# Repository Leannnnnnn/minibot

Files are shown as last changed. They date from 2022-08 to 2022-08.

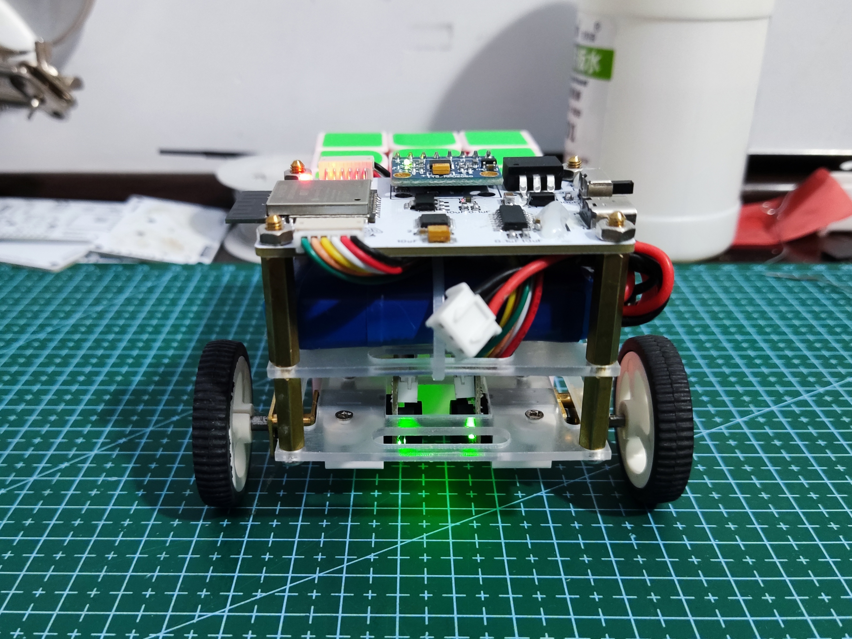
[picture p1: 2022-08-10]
doc/img/6.jpg

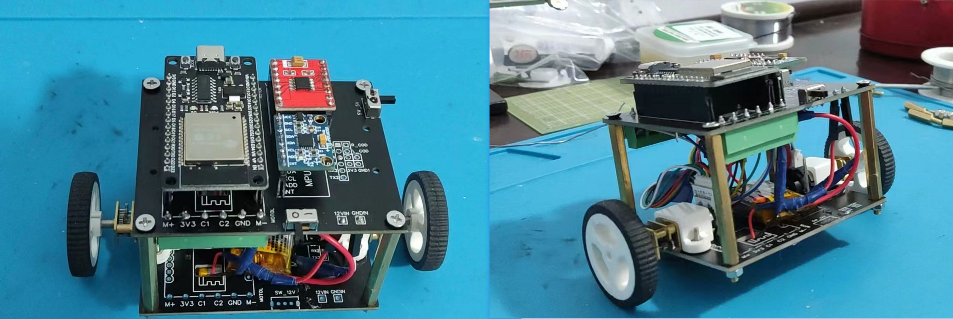
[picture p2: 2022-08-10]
doc/img/8png.png

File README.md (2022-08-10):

# minibot

> 最新内容在master分支\
> 详细说明请查看立创开源链接：[https://oshwhub.com/leannn/minibot](https://oshwhub.com/leannn/minibot)

## 1.项目介绍
### 1.0 前言
平衡车几乎是每个人入坑电子DIY的必做项目，包括了传感器采集处理、电机运动控制、pid算法调节等许多领域，同时兼顾专业性和趣味性，非常适合作为入门练习项目。本项目经过几次版本迭代（见后续介绍），最后确定为当前的形态，在外形结构和软件控制方面实现了比较好的平衡，外观小巧，运动性能卓越。

### 1.1 基本介绍
使用ESP32-WROOM作为主控芯片，MPU6050六轴加速度传感器模块获取姿态信息，DRV8833芯片驱动电机运动，提供较大电流，电机选用N20减速电机，带有AB相霍尔编码器用于测量转速。供电方面选用7.4V锂电池(2s)，经三端线性稳压器LM1084稳压至5V再使用1117稳压至3.3V给ESP32供电。

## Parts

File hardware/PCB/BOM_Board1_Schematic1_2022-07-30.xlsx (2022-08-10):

No. | Quantity | Device | Designator | Footprint | Value | Manufacturer Part | Manufacturer | Supplier Part | Supplier | Pins
1 | 3 | CAP_0603 | C1,C6,C13 | C0603 | 100nF |  |  |  |  | 2
2 | 5 | CAP_0603 | C2,C3,C5,C7,C9 | C0603 | 10uF |  |  |  |  | 2
3 | 1 | CAP_1206 | C4 | C1206 | 22uF |  |  |  |  | 2
4 | 1 | CAP_0603 | C8 | C0603 | 0.1uF |  |  |  |  | 2
5 | 1 | CAP_0603 | C10 | C0603 | 1uF |  |  |  |  | 2
6 | 1 | CAP_0603 | C11 | C0603 | 2.2uF |  |  |  |  | 2
7 | 1 | CAP_0603 | C12 | C0603 | 10nF |  |  |  |  | 2
8 | 2 | ZH1.5-6AW | CN1,CN2 | CONN-TH_ZH1.5-6AW |  | ZH1.5-6AW | CAX(创都) | C722927 | LCSC | 6
9 | 1 | SS14S-SMA | D1 | SMA_L4.3-W2.6-LS5.0-RD |  | SS14S-SMA |  | C9900003094 | LCSC | 2
10 | 1 | A2541WV-2P | H1 | HDR-TH_P2.54-H-M_A2541WV-2P |  | A2541WV-2P | CJT(Changjiang Connectors) | C225477 | LCSC | 2
11 | 1 | LED_0603-R | LED1 | LED0603-RD_BLUE |  |  |  | C72044 |  | 2
12 | 2 | 2N3904(SOT-23) | Q1,Q2 | SOT-23-3_L2.9-W1.3-P1.90-LS2.4-TR |  |  |  |  |  | 3
13 | 4 | Res_0603 | R1,R2,R6,R7 | R0603 | 10K |  |  |  |  | 2
14 | 2 | Res_0603 | R3,R4 | R0603 | 120R |  |  |  |  | 2
15 | 1 | Res_0603 | R5 | R0603 | 1k |  |  |  |  | 2
16 | 1 | SK-12D07-L5-B | SW1 | SW-TH_SK-12D02-VG5 |  |  |  |  |  | 5
17 | 1 | ESP32-WROOM-32 | U1 | WIFIM-SMD_ESP-32S |  |  |  |  |  | 39
18 | 1 | CH340C | U2 | SOP-16_L10.0-W3.9-P1.27-LS6.0-BL |  |  |  |  |  | 16
19 | 1 | AMS1117-3.3V | U3 | SOT-223-4_L6.5-W3.5-P2.30-LS7.0-BR |  |  |  |  |  | 4
20 | 1 | C3528 | U4 | CAP-SMD_L3.5-W2.8-FD | 10uF/25V | C3528 |  | C9900021806 | LCSC | 2
21 | 1 | MPU6050 | U6 | MPU6050 |  |  |  |  |  | 8
22 | 1 | LM1084S-5.0/TR | U7 | TO-263-3_L8.6-W10.2-P2.54-LS14.4-TL |  | LM1084S-5.0/TR | HGSEMI(华冠) | C259973 | LCSC | 4
23 | 1 | DRV8833PWP | U8 | ETSSOP-16_L5.0-W4.4-P0.65-LS6.4-BL-EP |  | DRV8833PWP | TI(德州仪器) | C1556089 | LCSC | 17
24 | 1 | TYPEC-304-BCP16 | USB1 | USB-C-SMD_TYPEC-304-BCP16 |  |  |  |  |  | 16

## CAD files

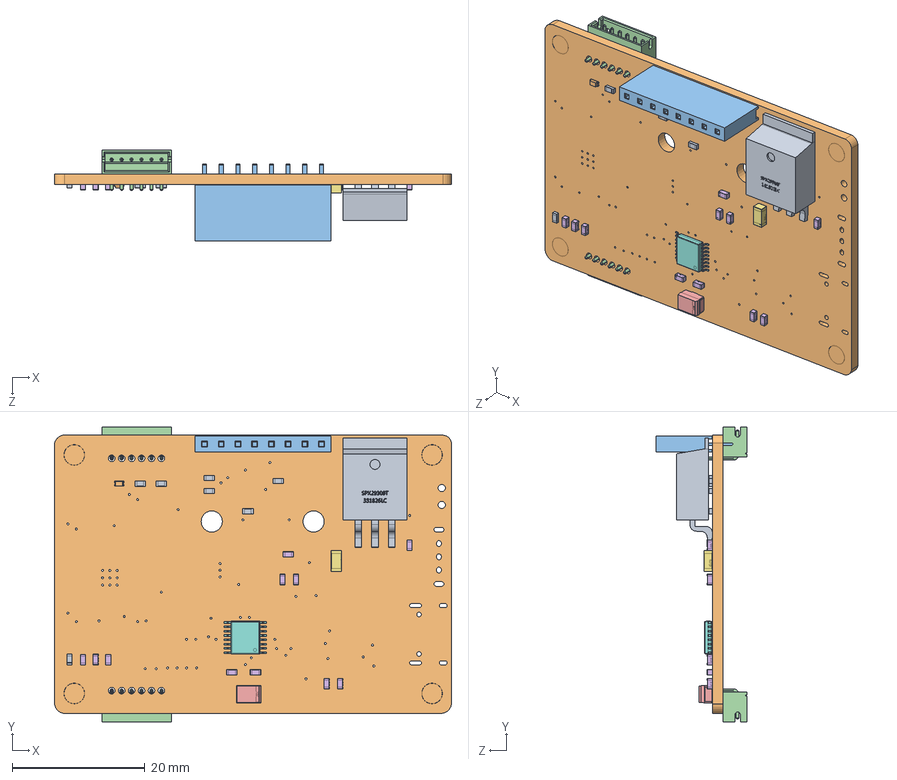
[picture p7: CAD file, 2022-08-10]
hardware/3D model/source/3D_PCB.SLDASM
59.9 x 44.5 x 13.7 mm
COMPOUND.step x 7
COMPOUND-0.step
SOLID.step
SOLID-1.step x 2
COMPOUND-2.step
=_[0_1_1_27].step x 11
=_[0_1_1_41].step
SOLID-3.step
COMPOUND-4.step
COMPOUND-5.step

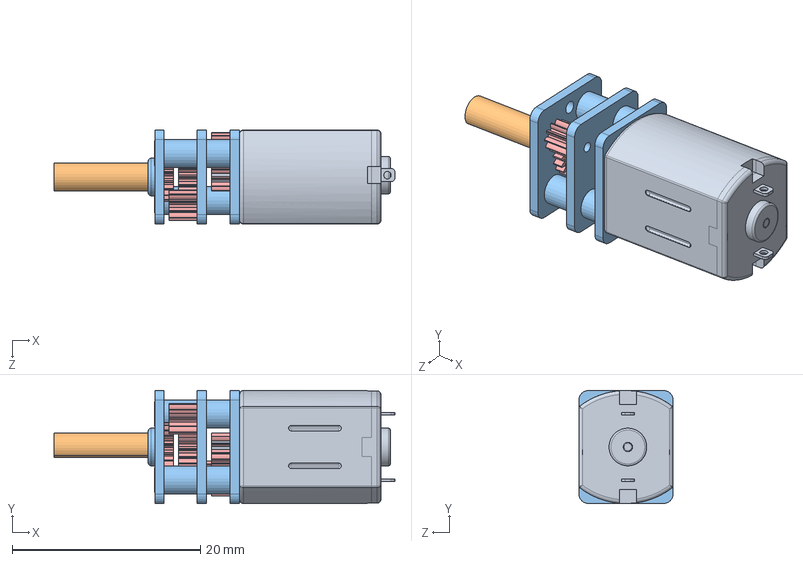
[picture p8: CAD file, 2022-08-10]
hardware/3D model/source/N20 Micro Metal Gearmotor 微型减速电机/n20 motor.SLDASM
36.2 x 12.0 x 10.0 mm
motor
n20_shaft
n20_gearbox
cross recessed countersunk head screws gb1 x 2
spur gear_gb x 6

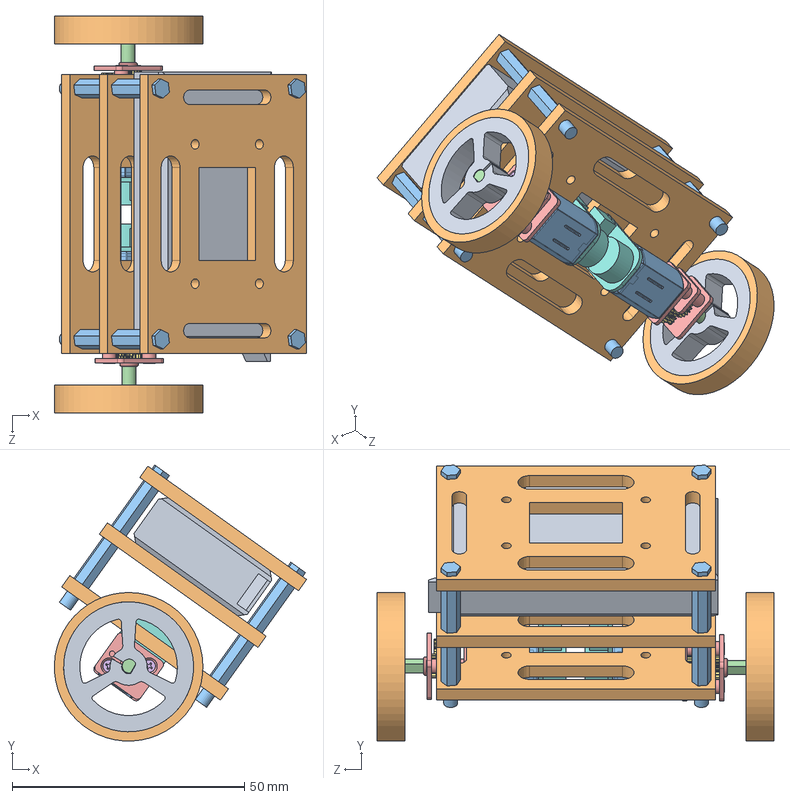
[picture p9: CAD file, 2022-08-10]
hardware/3D model/轮胎整体.SLDASM
54.3 x 59.4 x 85.4 mm
轮胎 x 2
轮胎外胎 x 2
motor x 2
n20_shaft x 2
n20_gearbox x 2
cross recessed countersunk head screws gb1 x 4
spur gear_gb x 12
零件5 x 2
电池2S
底板 x 3
铜柱 x 4

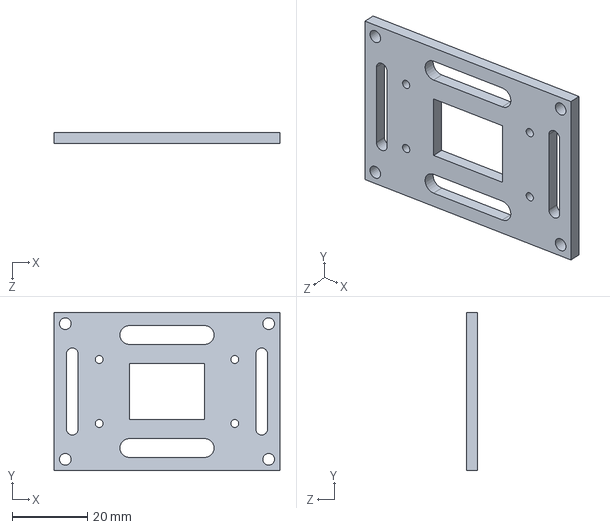
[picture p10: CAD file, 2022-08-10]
hardware/3D model/底板.SLDPRT
60.0 x 42.0 x 3.00 mm

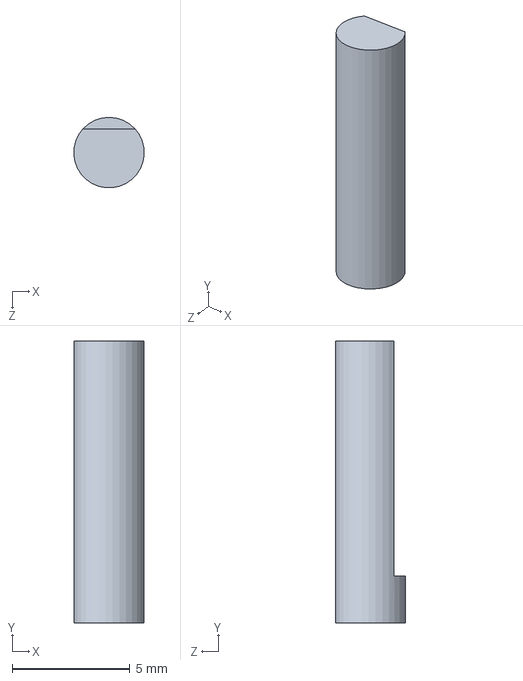
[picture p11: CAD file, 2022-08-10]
hardware/3D model/source/N20 Micro Metal Gearmotor 微型减速电机/n20_shaft.SLDPRT
3.00 x 12.0 x 2.99 mm

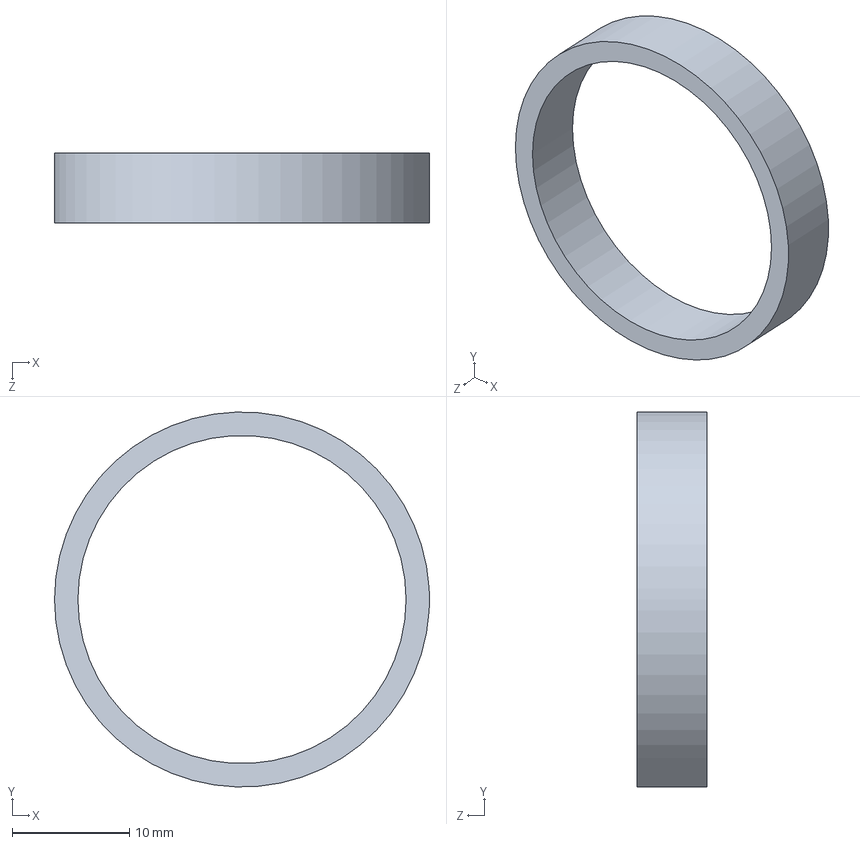
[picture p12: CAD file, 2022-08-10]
hardware/3D model/轮胎外胎.SLDPRT
32.0 x 32.0 x 6.00 mm

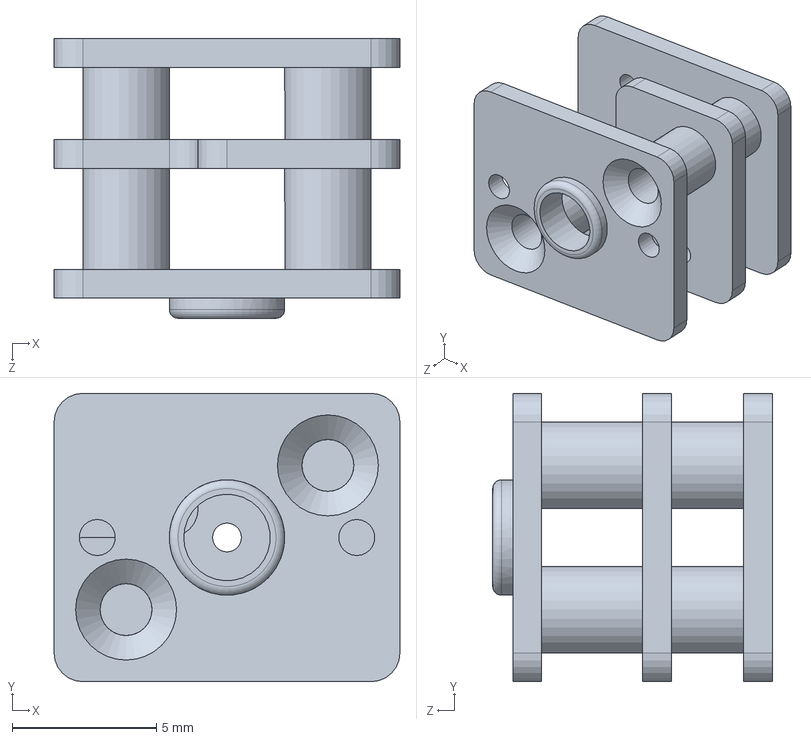
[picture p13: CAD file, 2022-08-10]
hardware/3D model/source/N20 Micro Metal Gearmotor 微型减速电机/n20_gearbox.SLDPRT
12.0 x 10.0 x 9.70 mm

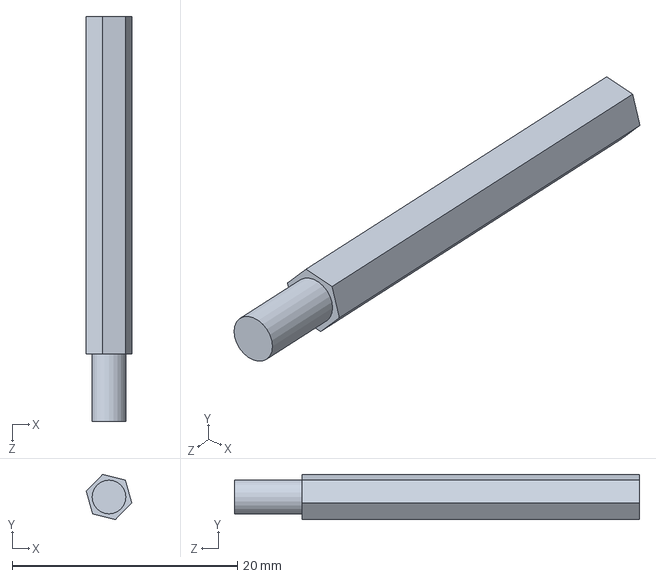
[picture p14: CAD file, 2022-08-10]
hardware/3D model/铜柱.SLDPRT
4.05 x 4.02 x 36.0 mm

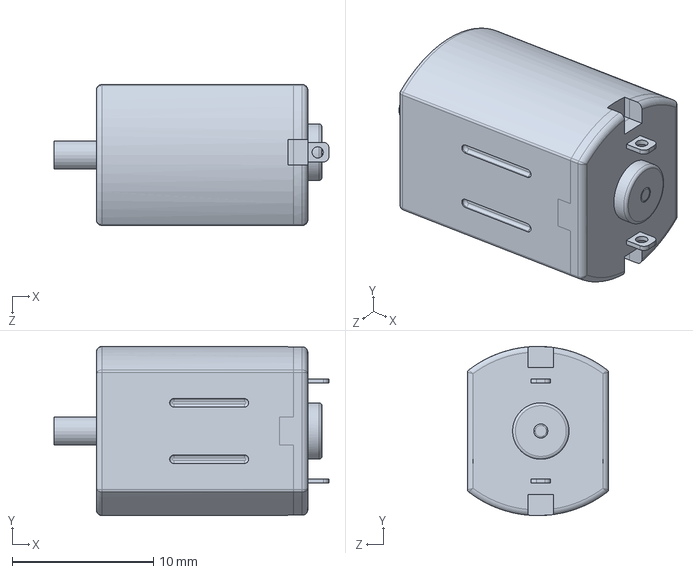
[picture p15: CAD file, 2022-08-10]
hardware/3D model/source/N20 Micro Metal Gearmotor 微型减速电机/motor.SLDPRT
19.5 x 12.0 x 10.0 mm

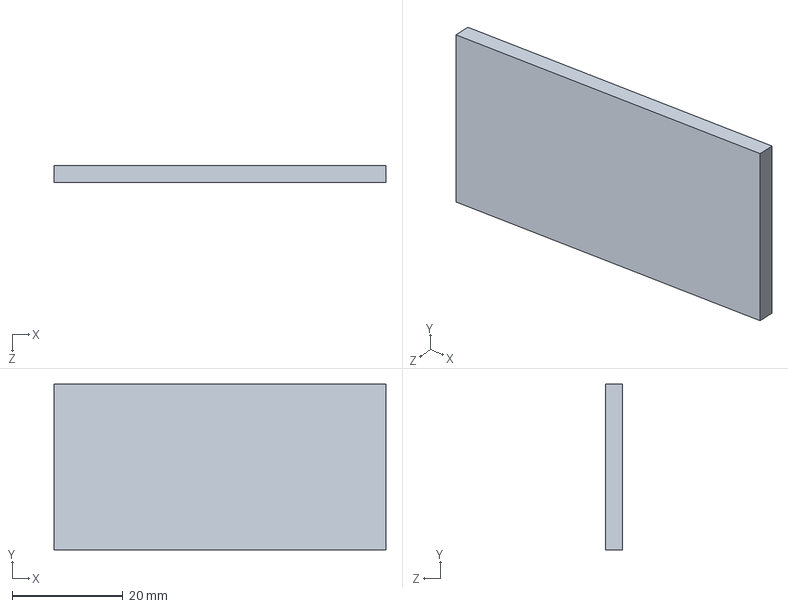
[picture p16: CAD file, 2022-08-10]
hardware/3D model/中板.SLDPRT
60.0 x 30.0 x 3.00 mm

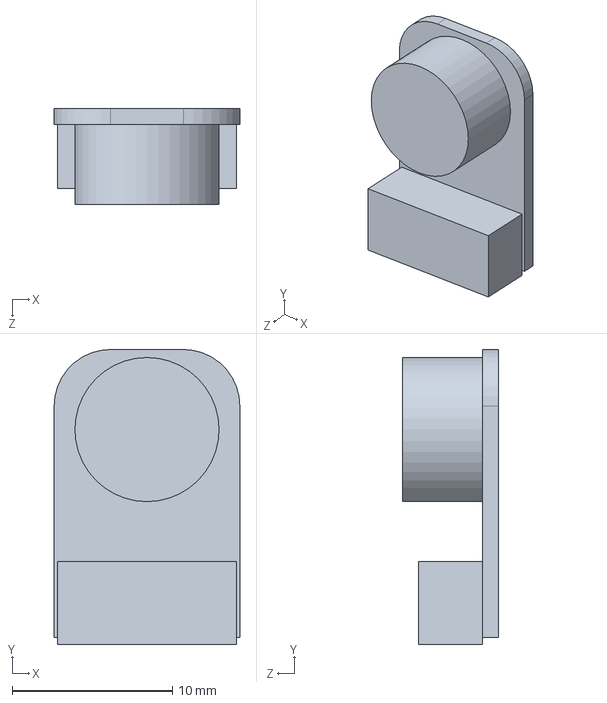
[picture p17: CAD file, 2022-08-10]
hardware/3D model/source/N20 Micro Metal Gearmotor 微型减速电机/零件5.SLDPRT
11.6 x 18.4 x 6.00 mm

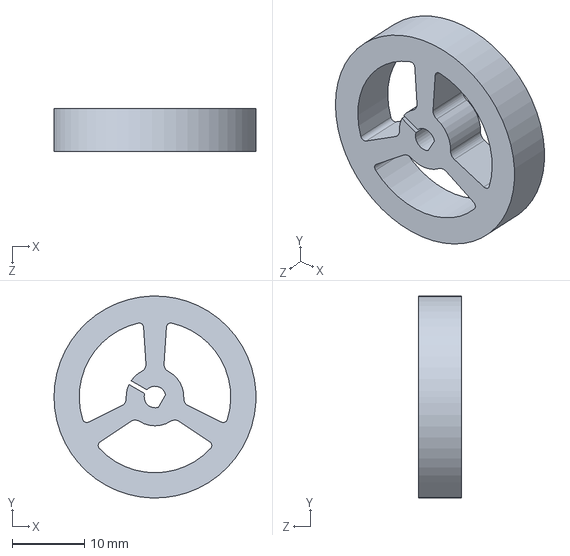
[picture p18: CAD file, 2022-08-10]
hardware/3D model/轮胎.SLDPRT
28.0 x 28.0 x 6.00 mm

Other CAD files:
hardware/3D model/source/带磁编码器的N20电机/n20ENCODED.SLDPRT
hardware/3D model/source/带磁编码器的N20电机/moto.dwg
hardware/3D model/亚克力切割.DWG
hardware/3D model/亚克力切割.SLDDRW

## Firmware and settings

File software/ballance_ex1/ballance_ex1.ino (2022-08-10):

/* ESP32平衡车miniBot
 *  
 * 平台：Arduino
 * Version: v1.1.0
 * Update: 2022-08-01
 * Author: Leannnus @bilibili.com & oshwhub.com
 * Link: https://oshwhub.com/leannn/minibot
 * 
**/


#include "PID.h"
#include <ArduinoJson.h>
#include <MPU6050_tockn.h>

#include "myBlueTooth.h"
#include "moto.h"
#include "mpu6050.h"

#define DEBUG 1  //串口输出调试信息
#define BTMODE 1 //蓝牙控制模式：0为调参模式，1为运动模式

/*************PID参数定义***********/
ArduPID pid_ang, pid_spd, pid_turn;

/*****角度环****/
double ang_set = -1.0;
double ang_in, ang_out;
double ang_p = 98.0;
double ang_i = 0.0;
double ang_d = 170.0;

/*****速度环*****/
double spd_set = 0.0;
double spdL_in, spdR_in, spdSum, spd_out;
double spd_p = 24.0;
double spd_i = 0.12;
double spd_d = 0.0;


double spd_turn = 0;  //差速转向值


char* recBuff; 
StaticJsonDocument<200> doc;  //JSON缓冲段分配
  
void setup() 
{
  // put your setup code here, to run once:
  Serial.begin(115200);
  BT_init();//蓝牙设备初始化--"miniBot"
  Serial.println("The device started, now you can pair it with bluetooth!");

  moto_pwm_init();//电机接口初始化

  encoder_init();//编码器接口初始化

  mpu6050_init();//mpu6050初始化

  
  pid_ang.begin(&ang_in, &ang_out, &ang_set, ang_p, ang_i, ang_d);  //初始化角度环PID参数

  pid_spd.begin(&spdSum, &spd_out, &spd_set, spd_p, spd_i, spd_d);  //初始化速度环PID参数
  
  pid_ang.setOutputLimits(-1000.0, 1000.0);  //设置PID输出PWM的幅度限制
  pid_ang.setWindUpLimits(-50.0,50.0);       //设置PID积分限幅

  pid_spd.setOutputLimits(-1000.0, 1000.0);
  pid_spd.setWindUpLimits(-100.0,100.0);

  moto_pwm_set(LEFT, 0);
  moto_pwm_set(RIGHT, 0);

}

void loop() 
{
    static float pwm_out;
    static int BTmode = 0;  //蓝牙运行模式
    static String strBuff;
    static String substr;  //字符串解析
    static uint16_t t=0, dt = 50;  //时间测量
    if((millis() - t)>dt){   //以dt(ms)为周期循环运行

      mpu6050_get_angel(&ang_in,'Y');  //获取Y轴角度值
      readEncoder(&spdL_in, &spdR_in); //获取编码器值

      spdSum = spdL_in + spdR_in;  //左右编码值累加
  
      pid_ang.compute();  //前倾PWM输出负值，后倾输出正值
      pid_spd.compute(); 
    
      pwm_out = -ang_out - spd_out ;  //角度环为负反馈，速度环为正反馈，符号由实际测试得到
                                      //一般来说，设置极性是改变的pid参数的符号，这里直接改变的是输出结果，达到的效果类似
      
      moto_pwm_set(LEFT, (pwm_out+spd_turn));   //差速转向，psd_turn大于0右转，小于0左转
      moto_pwm_set(RIGHT, (pwm_out-spd_turn));

      if(abs(ang_in - ang_set)>40){  //偏角过大时则电机停止转动
          moto_pwm_set(LEFT, 0);
          moto_pwm_set(RIGHT, 0);
          pid_ang.reset();
          pid_spd.reset();
      }
      
#if DEBUG
      pid_ang.debug(&Serial, "angle", PRINT_INPUT    | // Can include or comment out any of these terms to print
                                       PRINT_OUTPUT   | // in the Serial plotter
                                       PRINT_SETPOINT |
                                       PRINT_BIAS     |
                                       PRINT_P        |
                                       PRINT_I        |
                                       PRINT_D);  
#endif
         
/* 蓝牙发送参数指令，使用JSON格式进行打包和解析，字符串格式："{"cmd":1,"data":[p,i,d]}" ,  (p、i、d为常数)
 * cmd=1：角度环pid设置
 * cmd=2：速度环pid设置
 * cmd=3：转向环pid(暂未添加)
 * cmd=4：角度平衡值, 发送格式： "{"cmd":4,"data":[angle]}" , (angle为常数)
 * cmd=5：速度值，同角度
 * cmd=6：转向值，同上
**/
      recBuff = getDataBT();
#if BTMODE == 0 //蓝牙调参模式
      DeserializationError error = deserializeJson(doc, recBuff); //Json字符解析
      if(!error){
        int cmd = doc["cmd"];
        switch(cmd){
          case 1:
            ang_p = doc["data"][0];
            ang_i = doc["data"][1];
            ang_d = doc["data"][2];
            pid_ang.begin(&ang_in, &ang_out, &ang_set, ang_p, ang_i, ang_d);
            sendStringBT("Set angle pid successful!\r\n");
            break;
    
         case 2:
            spd_p = doc["data"][0];
            spd_i = doc["data"][1];
            spd_d = doc["data"][2];
                        
            pid_spd.begin(&spdSum, &spd_out, &spd_set, spd_p, spd_i, spd_d);  //初始化速度环PID参数
            
            sendStringBT("Set speed pid successful!\r\n");
            break;
    
          case 3:
            break;
          case 4:
            ang_set = doc["data"][0];
            sendStringBT("Set angle point successful!\r\n");
            break;
          case 5:
            spd_set = doc["data"][0];
            sendStringBT("Set speed point successful!\r\n");
            break;
          case 6:
            spd_turn = doc["data"][0];
            if(spd_turn>0)
              sendStringBT("Turn right!\r\n");
            if(spd_turn<0)
              sendStringBT("Turn left!\r\n");
          break;
          default:break;
        }    
      }
      
#else /**摇杆控制模式，接收蓝牙数据格式:"{X10Y10}"
        *手机上位机APP见工程链接附件
        *原程序为横屏，此处使用竖屏操作摇杆，因此需要X、Y坐标转换，均取负号
       **/
      strBuff=recBuff;  

      substr = strBuff.substring(strBuff.indexOf("X")+1,strBuff.indexOf("Y"));  //读取速度值:X和Y中间的值
      int temp_spd=0;
      
      temp_spd = -(substr.toInt());  //调节运动速度，取相反值翻转方向
      spd_set = constrain(temp_spd, -20, 20);  //速度限制
      
      Serial.print(substr); //调试输出
      Serial.print(",");
      
      substr = strBuff.substring(strBuff.indexOf("Y")+1,strBuff.indexOf("}"));  //读取转向值
      spd_turn = - substr.toInt();  //调节转向角，同样取相反值
      
      Serial.println(substr);  //调试用
#endif    
      
      t = millis();
    }
}

/*
  char json[100];
  int i =0;
  while(Serial.available() > 0){
    json[i++]=Serial.read();
  }
  deserializeJson(doc, json); //Json字符解析

*/

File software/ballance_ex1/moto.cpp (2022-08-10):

/**moto.cpp + moto.h
 * 功能：直流电机控制函数，包括基于ledc库的pwm调速功能和编码器计数值获取功能
 * 说明：接口部分通过宏定义配置，可结合实际使用管脚进行配置
 */


#include "moto.h"

void left_counter_encoder1();//读取左编码器脉冲数
void right_counter_encoder1();//读取右编码器脉冲数
void left_counter_encoder2();//读取左编码器脉冲数
void right_counter_encoder2();//读取右编码器脉冲数

/*使用ESP32LEDC库函数配置为pwm输出模式，16个通道：0-7为高速模式，8-15为低速模式 */
void moto_pwm_init()
{
  ledcSetup(8, 1000, 10);  //设置LEDC通道8频率为1000，分辨率为10位，即占空比可选0~1023
  ledcAttachPin(PWMR1, 8); //绑定通道8输出IO口为PWMR1
  ledcSetup(9, 1000, 10);  //通道9，右边电机反向通道
  ledcAttachPin(PWMR2, 9); 

  ledcSetup(10, 1000, 10);  //通道10,左边电机正向通道
  ledcAttachPin(PWML1, 10); 
  ledcSetup(11, 1000, 10);  //通道11,左边电机反向通道
  ledcAttachPin(PWML2, 11); 
}


/* 根据pwm输出电机转速，适用于驱动芯片DRV8833，正反方向根据pwm正负选择*/
void moto_pwm_set(uint8_t moto, float pwm)
{ 
  pwm = (int)pwm;  //转换为整形数据
  if(moto==LEFT){
    if(pwm<0){
      ledcWrite(10, -pwm); //设置输出PWM占空比
      ledcWrite(11, 0);
    }
    else{
      ledcWrite(11, pwm); //设置输出PWM占空比
      ledcWrite(10, 0);
    }
  }
  else{
    if(pwm<0){
      ledcWrite(9, -pwm); //设置输出PWM占空比
      ledcWrite(8, 0);
    }
    else{
      ledcWrite(9, 0);
      ledcWrite(8, pwm); //设置输出PWM占空比
    }
  }
}


volatile long Rcounter=0; // 右轮脉冲计数  该变量用于存储编码器的值，所以用类型修饰符volatile；
volatile long Lcounter=0; // 左轮脉冲计数  该变量用于存储编码器的值，所以用类型修饰符volatile；

 /***************** 编码器初始化 *****************/
void encoder_init()
{
  pinMode(RCODE1, INPUT);    
  pinMode(LCODE1, INPUT);   
  pinMode(RCODE2, INPUT);    
  pinMode(LCODE2, INPUT);   
  attachInterrupt(RCODE1, right_counter_encoder1, RISING);//设置编码器R上升沿中断
  attachInterrupt(LCODE1, left_counter_encoder1, RISING);//设置编码器L上升沿中断
  attachInterrupt(RCODE2, right_counter_encoder2, RISING);//设置编码器R上升沿中断
  attachInterrupt(LCODE2, left_counter_encoder2, RISING);//设置编码器L上升沿中断  
  interrupts();                      //打开外部中断
  Rcounter = 0;
  Lcounter = 0;
}

/************ 编码器计数，中断回调函数***********/
void right_counter_encoder1()
{
    if(digitalRead(RCODE2) == HIGH){ //判断此时的B相电平，为高则说明是前进
      Rcounter++;  //前进则计数值增加
    }
    else
      Rcounter--; //后退则计数值减少
}

void right_counter_encoder2()  //判断此时的A相电平，为低则说明是前进
{
    if(digitalRead(RCODE1) == LOW){
      Rcounter++;
    }
    else
      Rcounter--;
}

void left_counter_encoder1() // 左轮A相计数
{  
    if(digitalRead(LCODE2) == HIGH){
      Lcounter++;
    }
    else
      Lcounter--;
}


void left_counter_encoder2() // 左轮B相计数
{  
    if(digitalRead(LCODE1) == LOW){
      Lcounter++;
    }
    else
      Lcounter--;
}
  

/************ 编码器读取函数***********/
//编码器输出  
void readEncoder(double* numR, double* numL)
{
  *numR = (double)Rcounter;
  *numL = (double)Lcounter;
  //数值清零，重新计数
  Rcounter = 0;
  Lcounter = 0;
}
